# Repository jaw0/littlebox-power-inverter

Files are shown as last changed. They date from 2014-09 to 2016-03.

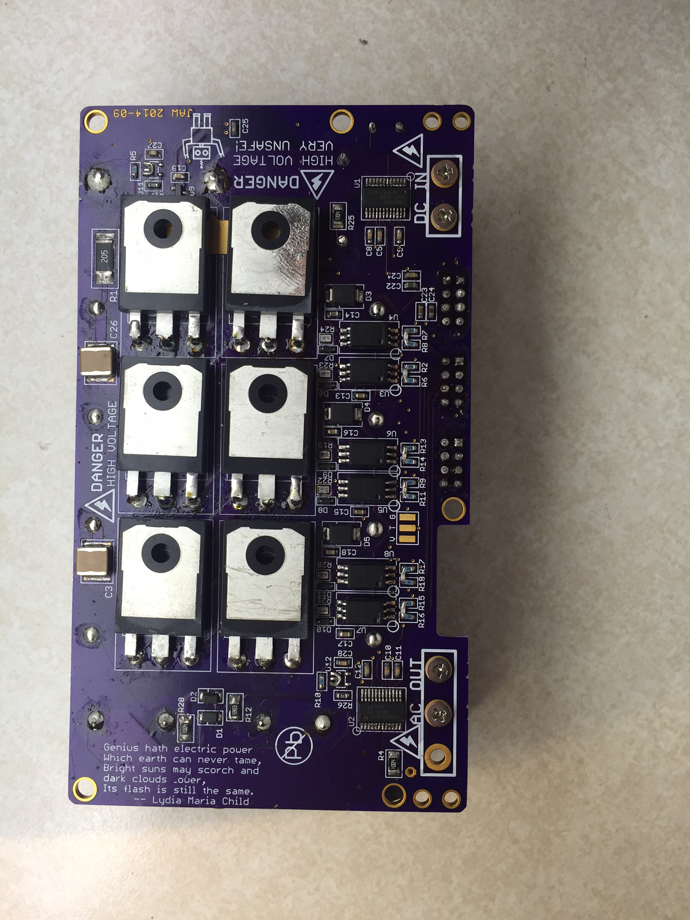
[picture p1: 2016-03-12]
img/IMG_0962.JPG

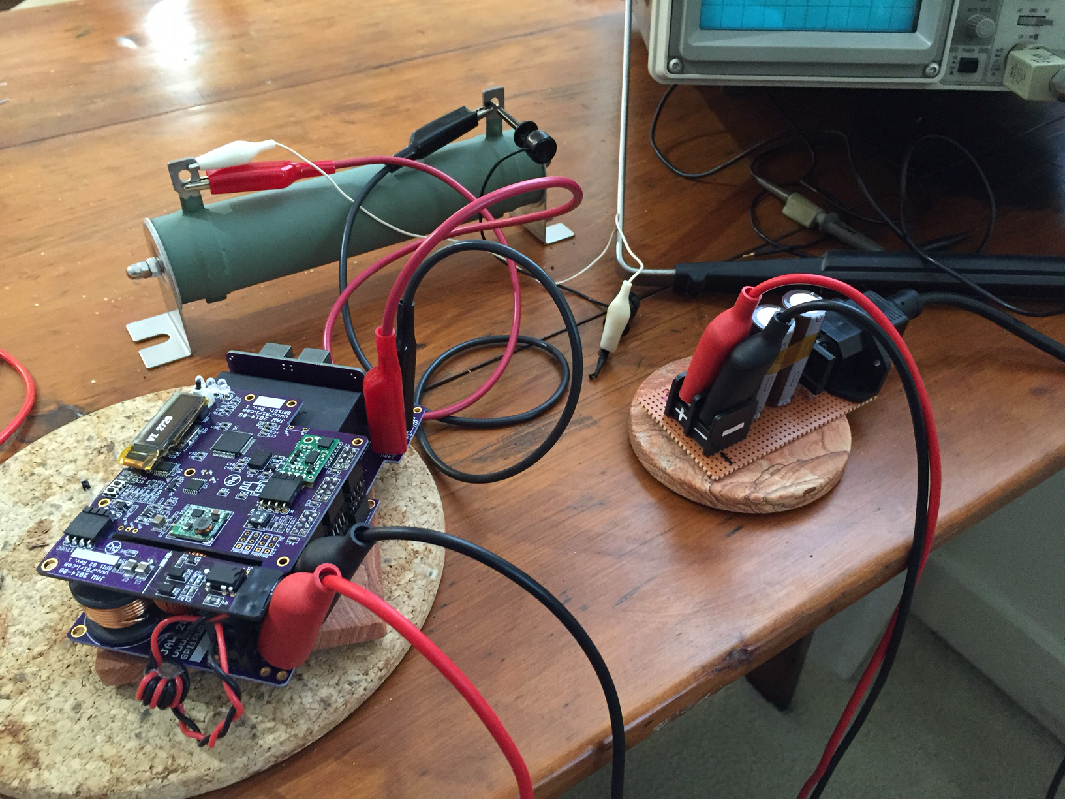
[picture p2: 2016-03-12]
img/IMG_0753.JPG

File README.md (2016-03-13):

google sponsored a contest, [the little box challenge,](https://www.littleboxchallenge.com)
to design a small, efficient, power inverter.

* Must be able to handle up to 2 kVA loads
* Must achieve a power density of equal to or greater than 50 W/in3
* Must be able to handle loads with power factors from 0.7–1, leading and lagging in an islanded mode
* Must be in a rectangular metal enclosure of no more than 40 in3
* Will be taking in 450 V DC power in series with a 10 Ω resistor
* Must output 240 V, 60 Hz AC single phase power
* Must have a total harmonic distortion + noise on both voltage and current of < 5%
* Must have an input ripple current of < 20%
* Must have an input ripple voltage of < 3%
* Must have a DC-AC efficiency of greater than 95%
* Must maintain a temperature of no more than 60°C during operation everywhere on the outside of the device that can be touched.

this is what I came up with. it did not win.

unlike the winning entry, this device uses only
standard, commercially available, off the shelf parts.

* * * * * * * * WARNING * * * * * * * *

This device contains potentially lethal voltages.

This device does not comply with consumer
electrical safety requirements.

DO NOT USE OR BUILD THIS UNLESS YOU ARE FAMILIAR WITH
THE SAFETY PRECAUTIONS FOR WORKING WITH HIGH VOLTAGE.

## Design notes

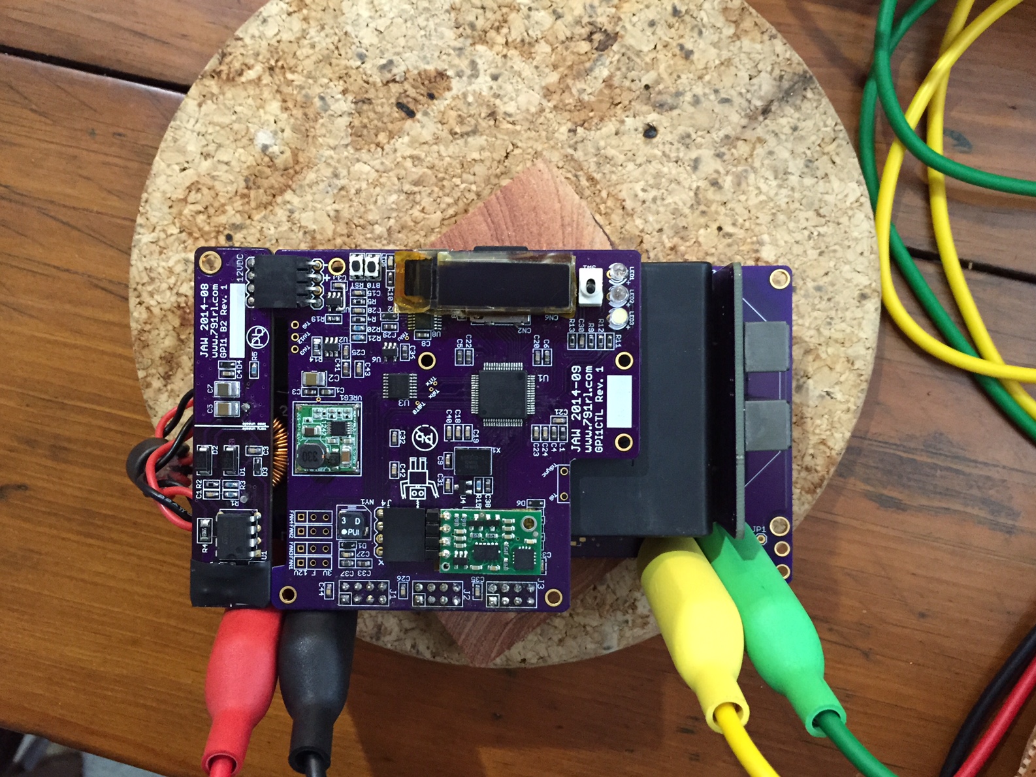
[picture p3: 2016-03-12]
img/inverter.jpg

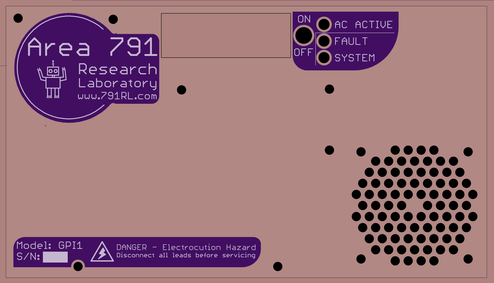
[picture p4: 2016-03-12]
img/cover.png

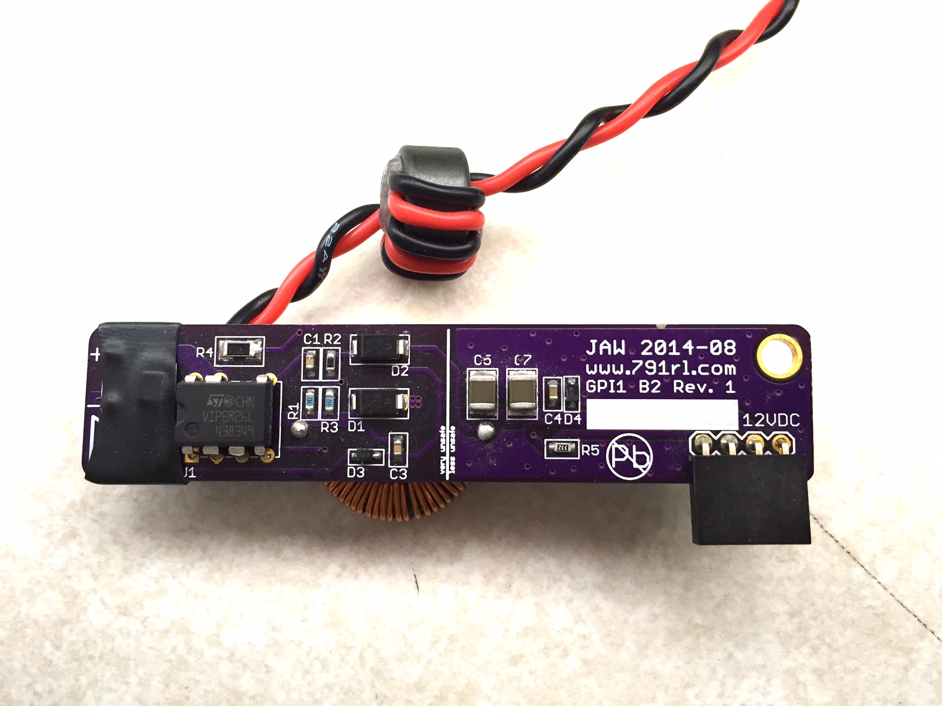
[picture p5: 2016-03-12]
img/powerbrd.jpg

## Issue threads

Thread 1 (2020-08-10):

questions

klasrocket, 2020-08-10:
hi.

been looking into this project to try to find what the lower limit for input voltage is, or maybe its only efficiency dropping?
while looking around I realized that there are 3 different output filters, are they just differnt iterations or is each one for a specific kind of load?
hope you got some time to help me clarify this.

jaw0, 2020-08-10:
the viper chip that steps the voltage down to 12V has a minimum (you'll have to look it up). in testing, I bypassed that and ran it on 12V, not efficient, but functional.

the different filters were just testing to get it smaller, still but good enough.

klasrocket, 2021-09-25:
Thanks for the previous clarifications! I still have not got to the point of starting to build a unit but just revisited this project again.
I have another question that I hope you might want to help me answering.
Do you think it would it be possible to run 3 of your inverters in sync with 120deg offset for 3phase output? My idea is to use some of the unused pins for serial communication, and let 1 of the inverters send the variable "cycle_step" to the other 2 instead of letting them increment that locally.

Closed 2020-08-10.

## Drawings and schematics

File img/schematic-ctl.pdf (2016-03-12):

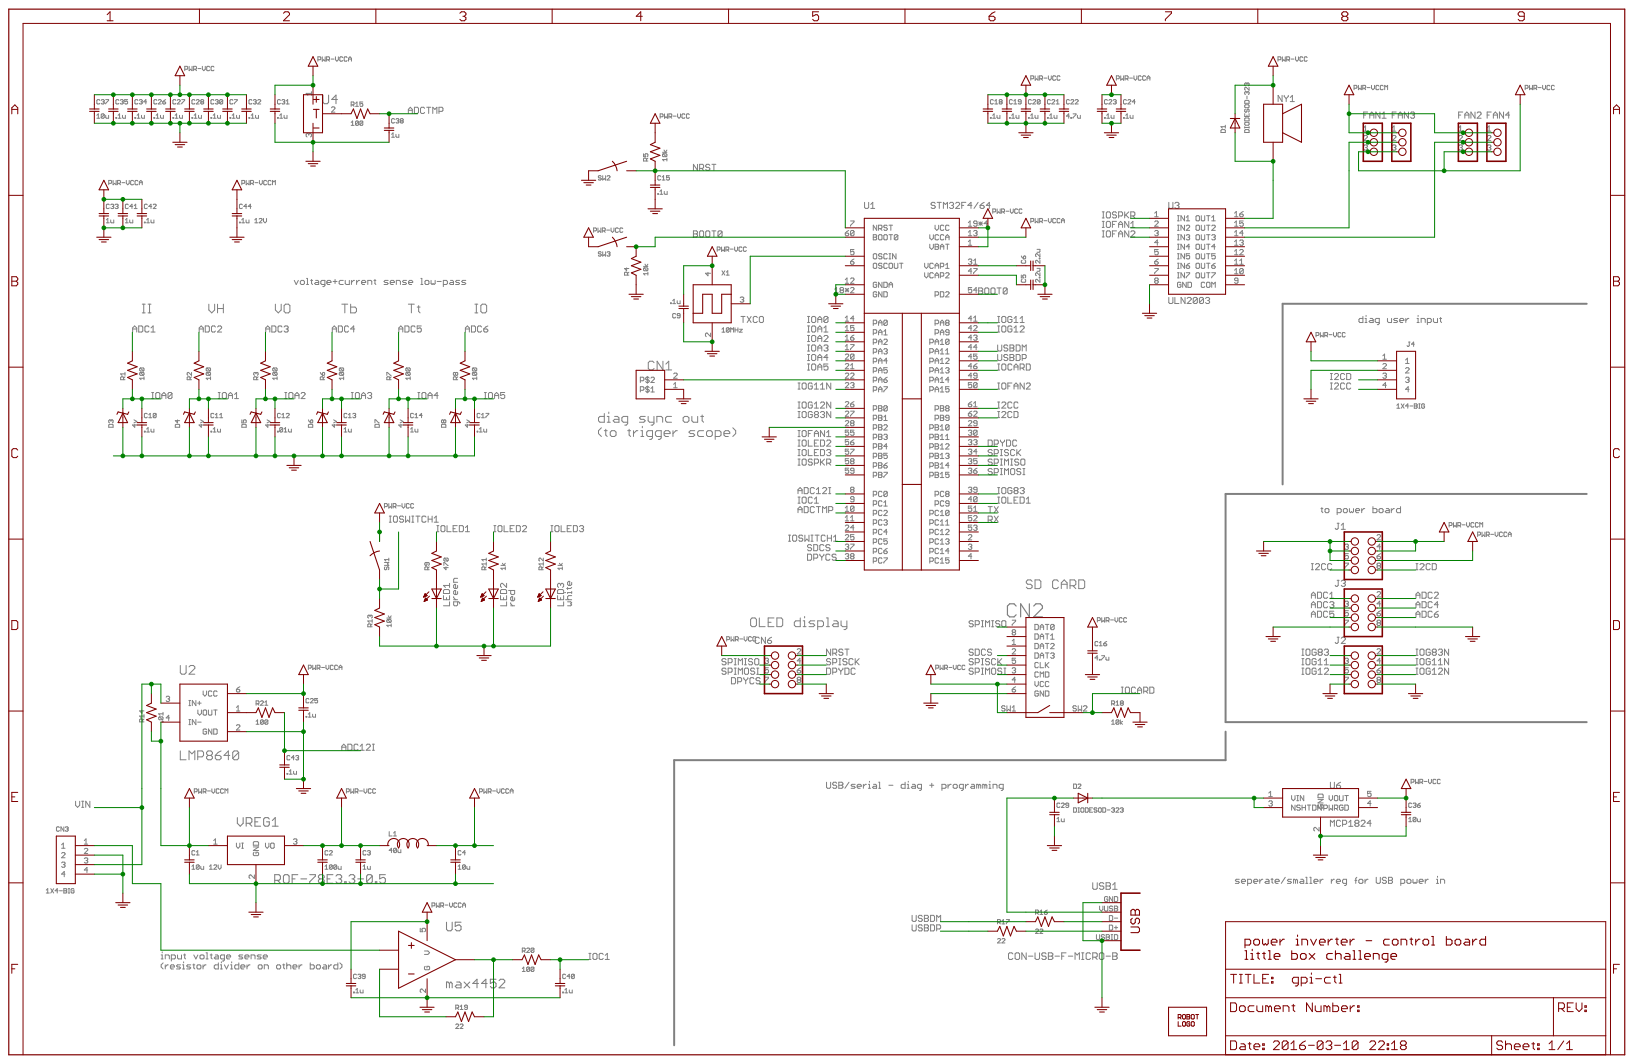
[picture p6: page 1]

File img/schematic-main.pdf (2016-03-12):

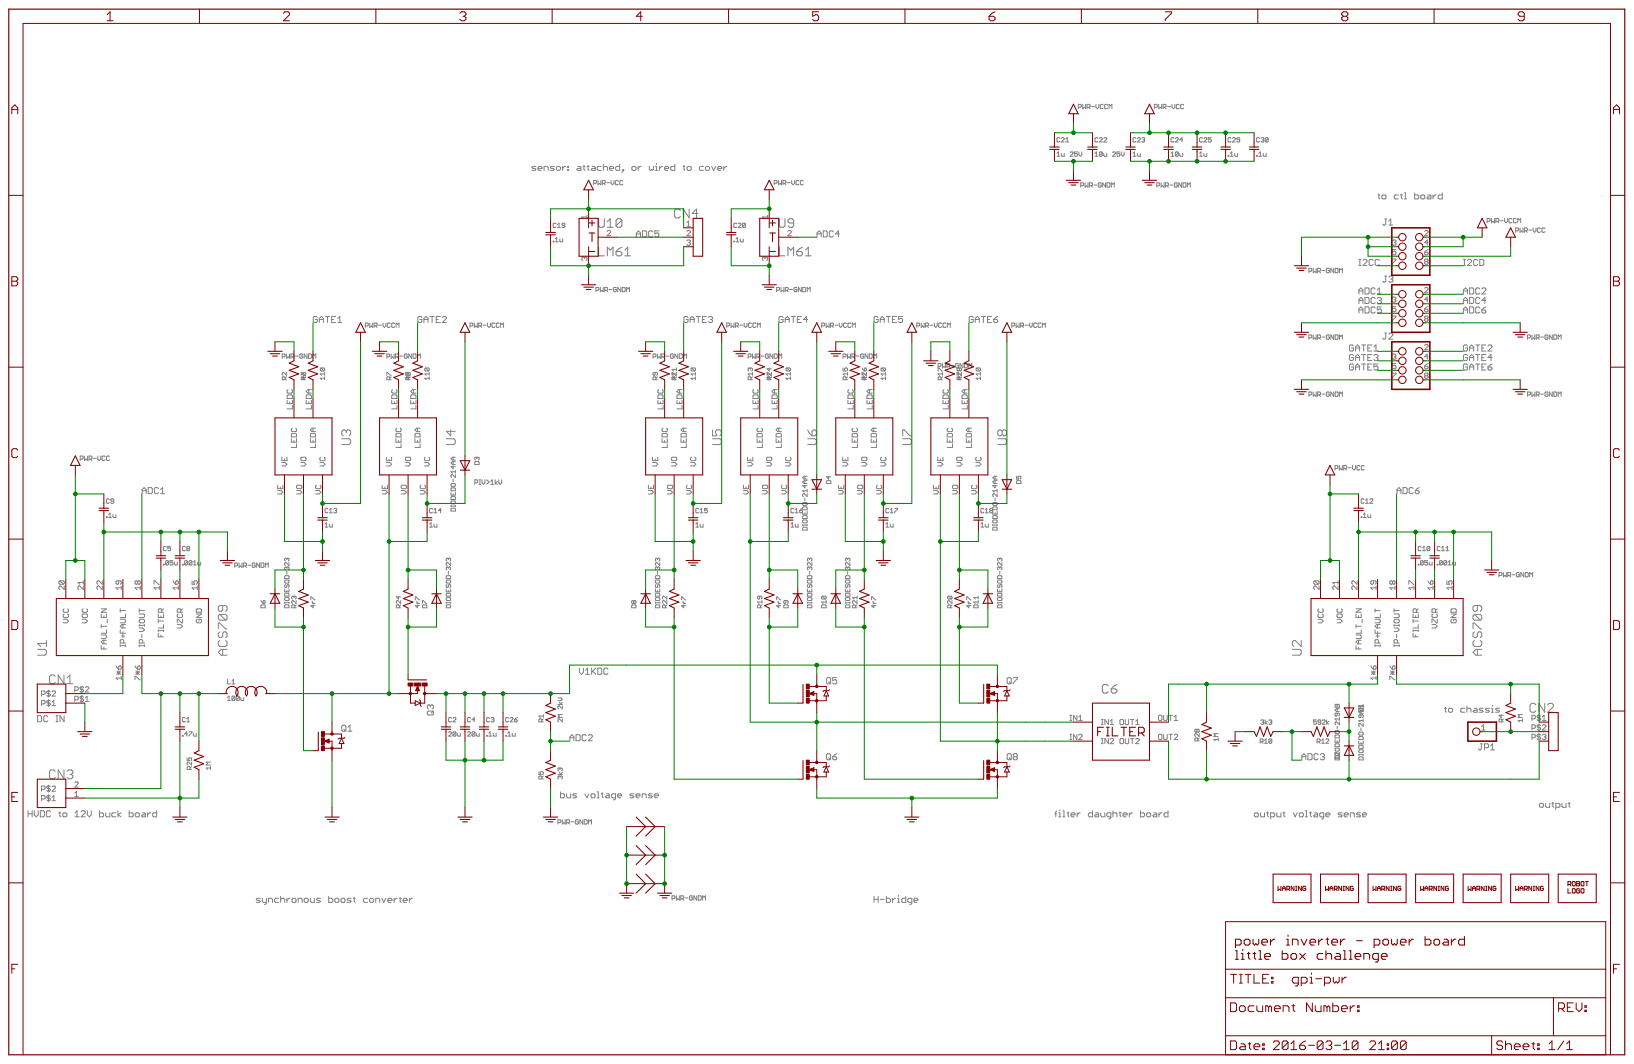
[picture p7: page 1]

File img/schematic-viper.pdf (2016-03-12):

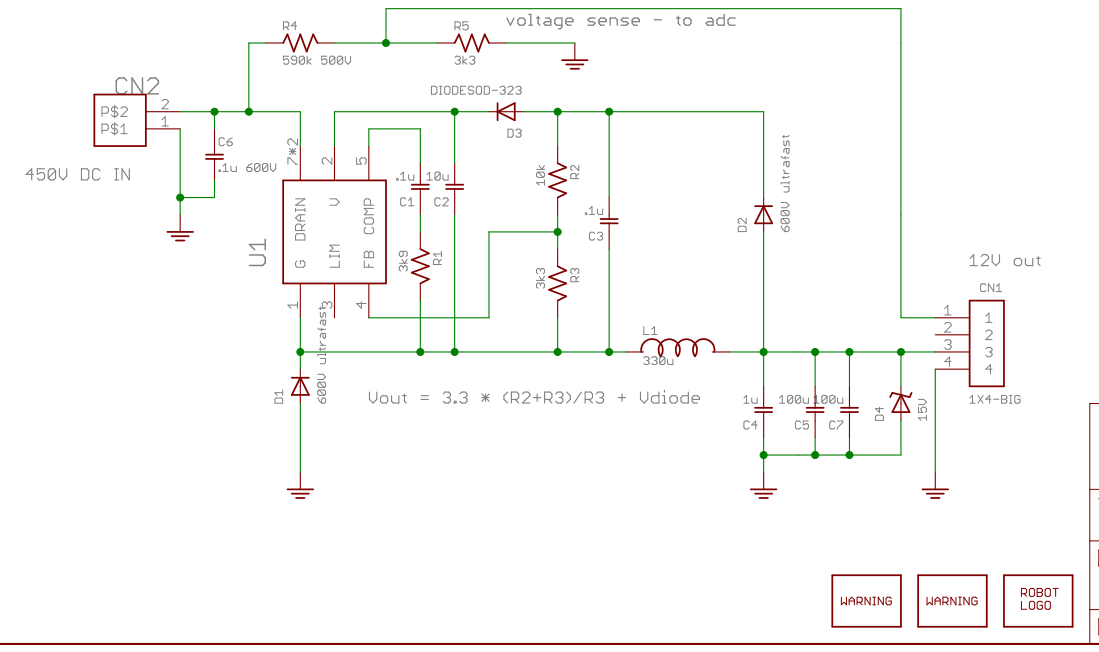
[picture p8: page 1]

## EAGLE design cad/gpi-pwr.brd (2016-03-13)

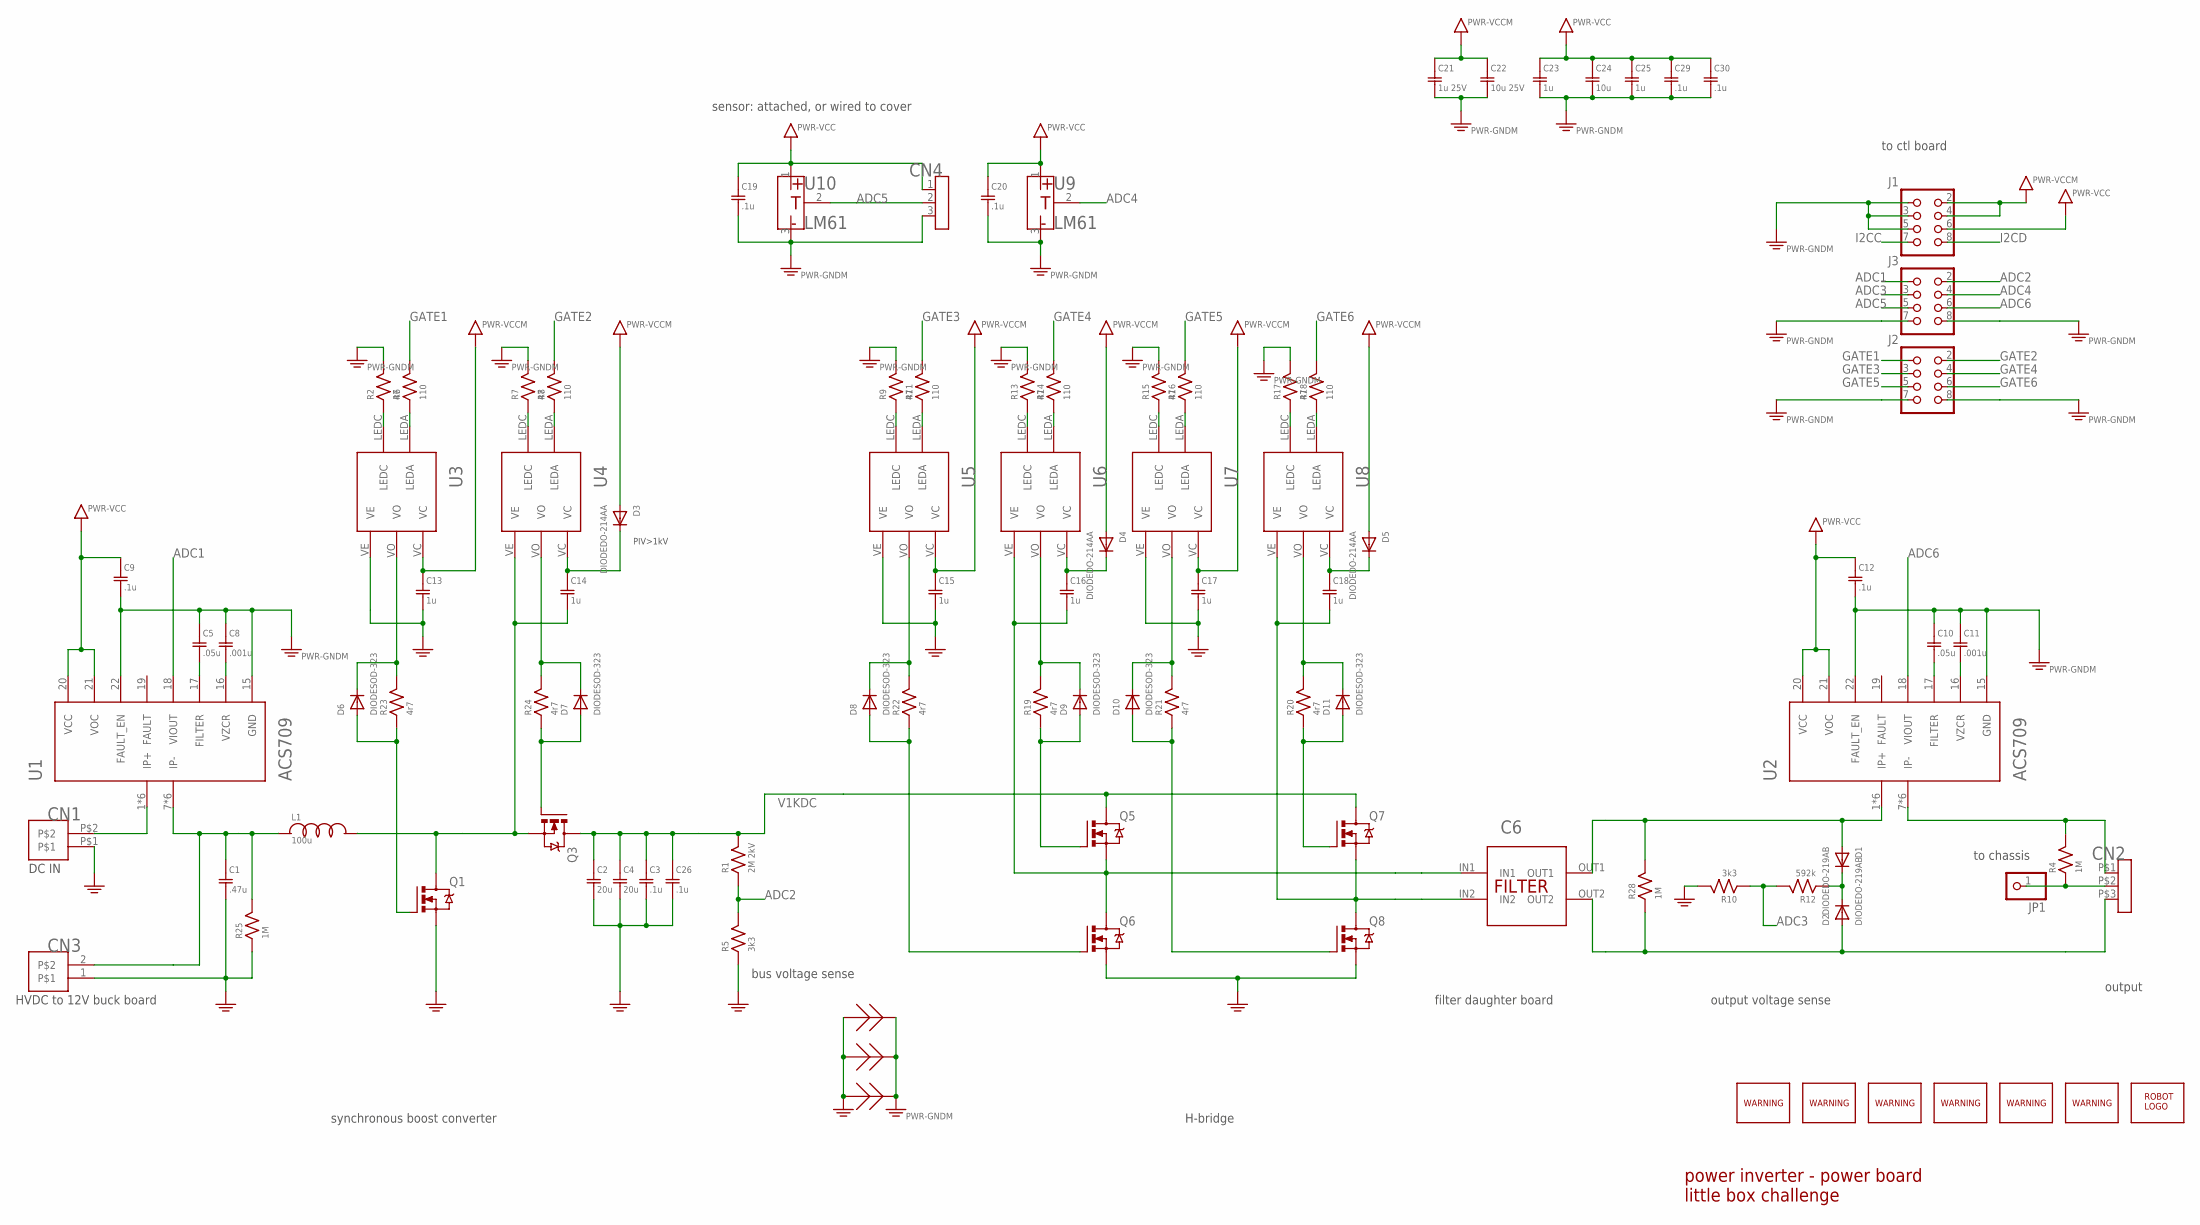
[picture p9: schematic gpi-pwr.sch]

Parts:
C1: .47u; R46KI333000N1M
C2, C4: 20u; MKP1848S62010JY5F
C3, C26: .1u; SMD2220
C5, C10: .05u; SMD0603
C6: FILTER; FILTER-B4R0
C8, C11: .001u; SMD0603
C9, C12, C19, C20, C29, C30: .1u; SMD0603
C13, C14, C15, C16, C17, C18, C23, C25: 1u; SMD0603
C21: 1u 25V; SMD0603
C22: 10u 25V; SMD0603
C24: 10u; SMD0603
CN1: HEADER-1X2; CONN-10AWG-2
CN2: HEADER-3X1; CONN-10AWG-3
CN3: HEADER-1X2.4; HEADER-1X2-THM-WIDE
CN4: HEADER-3X12MM; HEADER-3X1-2SMD
D1, D2: DIODEDO-219AB; DO-219AB
D3, D4, D5: DIODEDO-214AA; DO-214AA
D6, D7, D8, D9, D10, D11: DIODESOD-323; SOD-323
J1, J2, J3: HEADER-2X4; HEADER-2X04
JP1: PINHD-1X1; 1X01
L1: 100u; AIRD03
Q1, Q3, Q5, Q6, Q7, Q8: C2M0160120D; TO-247-3-DOWN
R1: 2M 2kV; SMD2512
R2, R7, R9, R13, R15, R17: 47; SMD0603
R4, R25, R28: 1M; SMD1206
R5, R10: 3k3; SMD0603
R6, R8, R11, R14, R16, R18: 110; SMD0603
R12: 592k; SMD1206
R19, R20, R21, R22, R23, R24: 4r7; SMD0508
U1, U2: ACS709; QSOP24
U3, U4, U5, U6, U7, U8: ACPL-P346P346; ACPL-P346
U9, U10: LM61; SOT-23
U$1: ROBOTMAN-LOGO
U$2, U$3, U$4, U$5, U$6, U$7: SYMBOL-WARNING
Z1, Z2, Z3: SHORT

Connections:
ADC1: J3.1, U1.18 (VIOUT)
ADC2: J3.2, R1.P$1, R5.2
ADC3: J3.3, R10.1, R12.2
ADC4: J3.4, U9.2 (OUT)
ADC5: CN4.2, J3.5, U10.2 (OUT)
ADC6: J3.6, U2.18 (VIOUT)
GATE1: J2.1, R6.2
GATE2: J2.2, R8.2
GATE3: J2.3, R11.2
GATE4: J2.4, R14.2
GATE5: J2.5, R16.2
GATE6: J2.6, R18.2
GND: C1.P$2, C2.2A, C2.2B, C3.P$2, C4.2A, C4.2B, C13.2, C15.2, C17.2, C26.P$2, CN1.P$1, CN3.1, Q1.3 (S), Q6.3 (S), Q8.3 (S), R5.1, R10.2, R25.1, U3.VE, U5.VE, U7.VE, Z1.P$1, Z2.P$1, Z3.P$1
GNDM: C5.1, C8.1, C9.2, C10.1, C11.1, C12.2, C19.2, C20.2, C21.2, C22.2, C23.2, C24.2, C25.2, C29.2, C30.2, CN4.3, J1.1, J1.3, J1.5, J2.7, J2.8, J3.7, J3.8, R2.2, R7.2, R9.2, R13.2, R15.2, R17.2, U1.15 (GND), U1.22 (FAULT_EN), U2.15 (GND), U2.22 (FAULT_EN), U9.3 (G), U10.3 (G), Z1.P$2, Z2.P$2, Z3.P$2
I2CC: J1.7
I2CD: J1.8
unnamed: CN1.P$2, U1.1 (IP+), U1.2 (IP+), U1.3 (IP+), U1.4 (IP+), U1.5 (IP+), U1.6 (IP+)
unnamed: D9.C, R19.P$2, U6.VO
unnamed: C14.2, L1.P$2, Q1.2 (D), Q3.3 (S), U4.VE
unnamed: D6.A, Q1.1 (G), R23.P$1
unnamed: D6.C, R23.P$2, U3.VO
unnamed: C1.P$1, CN3.2, L1.P$1, R25.2, U1.7 (IP-), U1.8 (IP-), U1.9 (IP-), U1.10 (IP-), U1.11 (IP-), U1.12 (IP-)
unnamed: D1.C, D2.C, R12.1
unnamed: CN2.P$1 (1), R4.2, U2.7 (IP-), U2.8 (IP-), U2.9 (IP-), U2.10 (IP-), U2.11 (IP-), U2.12 (IP-)
unnamed: CN2.P$2 (2), JP1.1, R4.1
unnamed: C5.2, U1.17 (FILTER)
unnamed: C8.2, U1.16 (VZCR)
unnamed: C10.2, U2.17 (FILTER)
unnamed: C6.IN1, C16.2, Q5.3 (S), Q6.2 (D), U6.VE
unnamed: C6.IN2, C18.2, Q7.3 (S), Q8.2 (D), U8.VE
unnamed: C11.2, U2.16 (VZCR)
unnamed: C14.1, D3.C, U4.VC
unnamed: D9.A, Q5.1 (G), R19.P$1
unnamed: D8.A, Q6.1 (G), R22.P$1
unnamed: D10.A, Q8.1 (G), R21.P$1
unnamed: D11.A, Q7.1 (G), R20.P$1
unnamed: R2.1, U3.LEDC
unnamed: C6.OUT1, D1.A, R28.2, U2.1 (IP+), U2.2 (IP+), U2.3 (IP+), U2.4 (IP+), U2.5 (IP+), U2.6 (IP+)
unnamed: C6.OUT2, CN2.P$3 (3), D2.A, R28.1
unnamed: C16.1, D4.C, U6.VC
unnamed: R6.1, U3.LEDA
unnamed: C18.1, D5.C, U8.VC
unnamed: R7.1, U4.LEDC
unnamed: R8.1, U4.LEDA
unnamed: R9.1, U5.LEDC
unnamed: R11.1, U5.LEDA
unnamed: R13.1, U6.LEDC
unnamed: R14.1, U6.LEDA
unnamed: R15.1, U7.LEDC
unnamed: R16.1, U7.LEDA
unnamed: R17.1, U8.LEDC
unnamed: R18.1, U8.LEDA
unnamed: D11.C, R20.P$2, U8.VO
unnamed: D8.C, R22.P$2, U5.VO
unnamed: D10.C, R21.P$2, U7.VO
unnamed: D7.C, R24.P$2, U4.VO
unnamed: D7.A, Q3.1 (G), R24.P$1
V1KDC: C2.1A, C2.1B, C3.P$1, C4.1A, C4.1B, C26.P$1, Q3.2 (D), Q5.2 (D), Q7.2 (D), R1.P$2
VCC: C9.1, C12.1, C19.1, C20.1, C23.1, C24.1, C25.1, C29.1, C30.1, CN4.1, J1.6, U1.20 (VCC), U1.21 (VOC), U2.20 (VCC), U2.21 (VOC), U9.1 (V), U10.1 (V)
VCCM: C13.1, C15.1, C17.1, C21.1, C22.1, D3.A, D4.A, D5.A, J1.2, J1.4, U3.VC, U5.VC, U7.VC

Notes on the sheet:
PIV>1kV
DC IN
HVDC to 12V buck board
to chassis
sensor: attached, or wired to cover
synchronous boost converter
H-bridge
output
output voltage sense
to ctl board
power inverter - power board little box challenge
filter daughter board
bus voltage sense

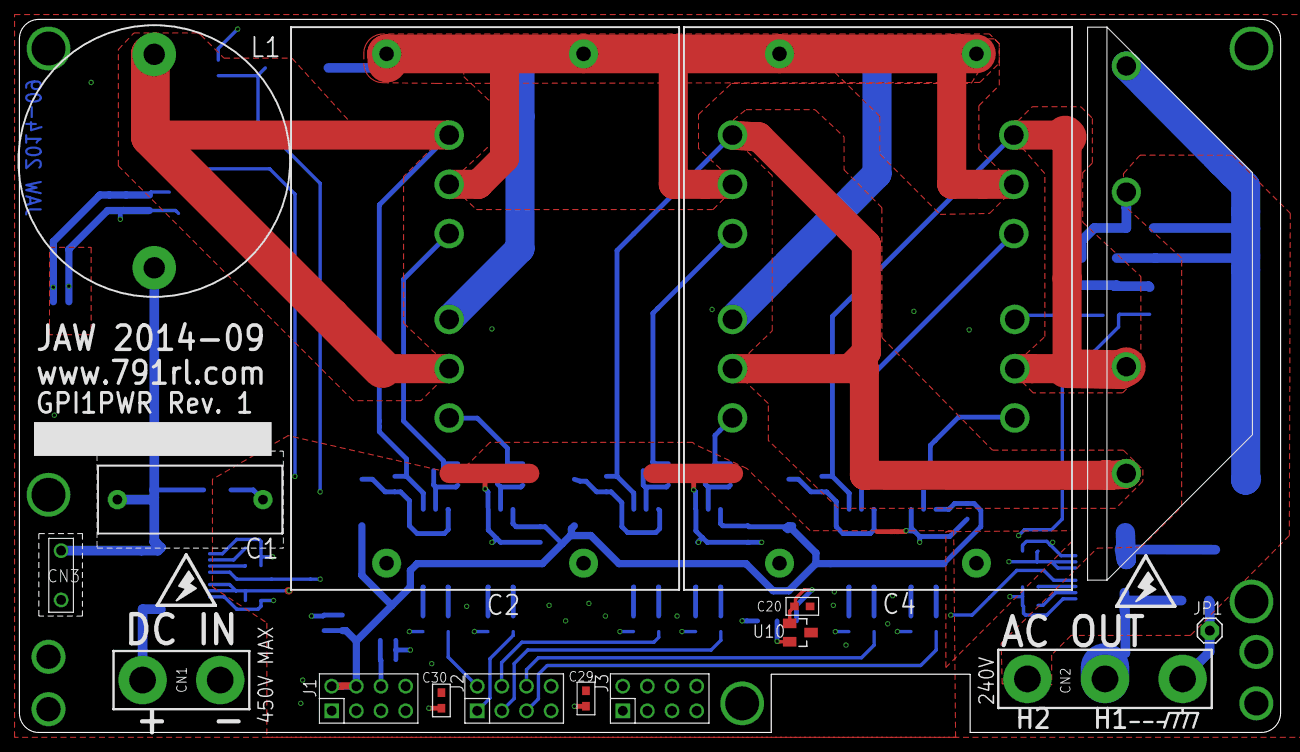
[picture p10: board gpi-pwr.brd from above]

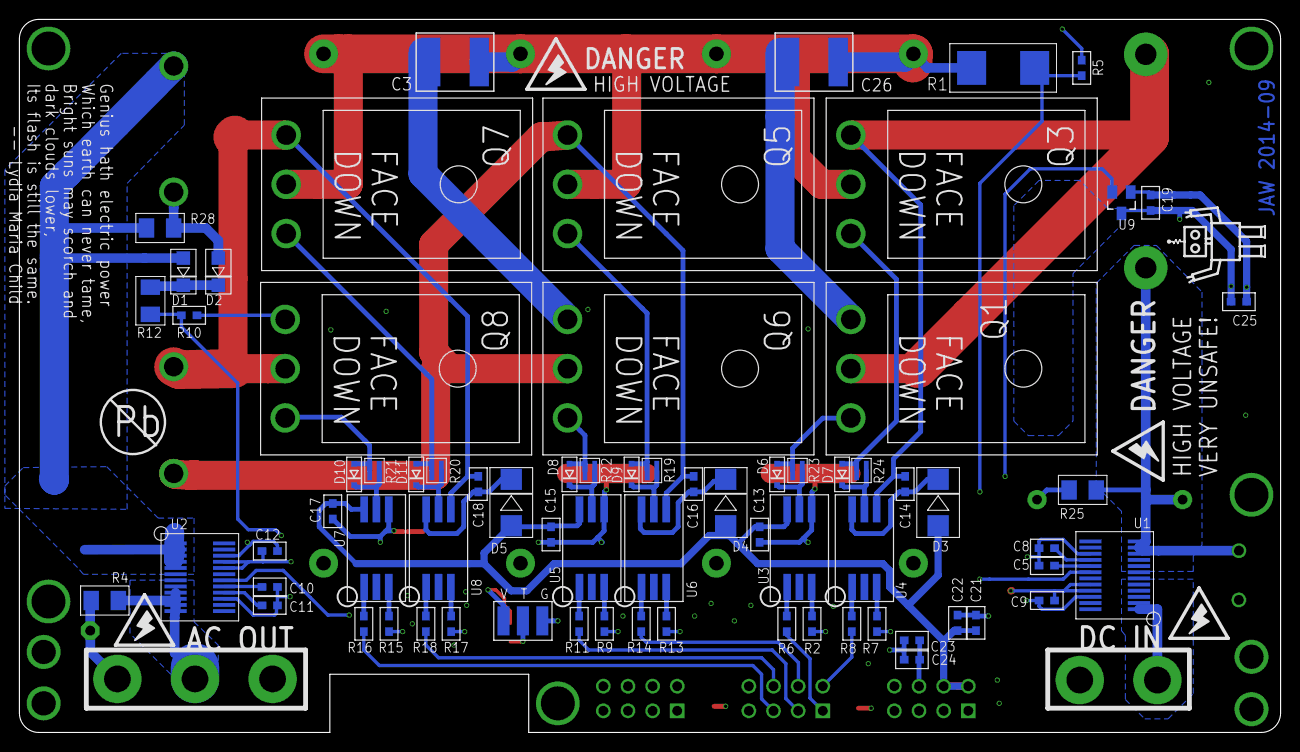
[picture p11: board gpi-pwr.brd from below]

Board: 4 copper layers, 130.0 x 73.5 mm, 98 parts (77 on the bottom side), 58 nets.

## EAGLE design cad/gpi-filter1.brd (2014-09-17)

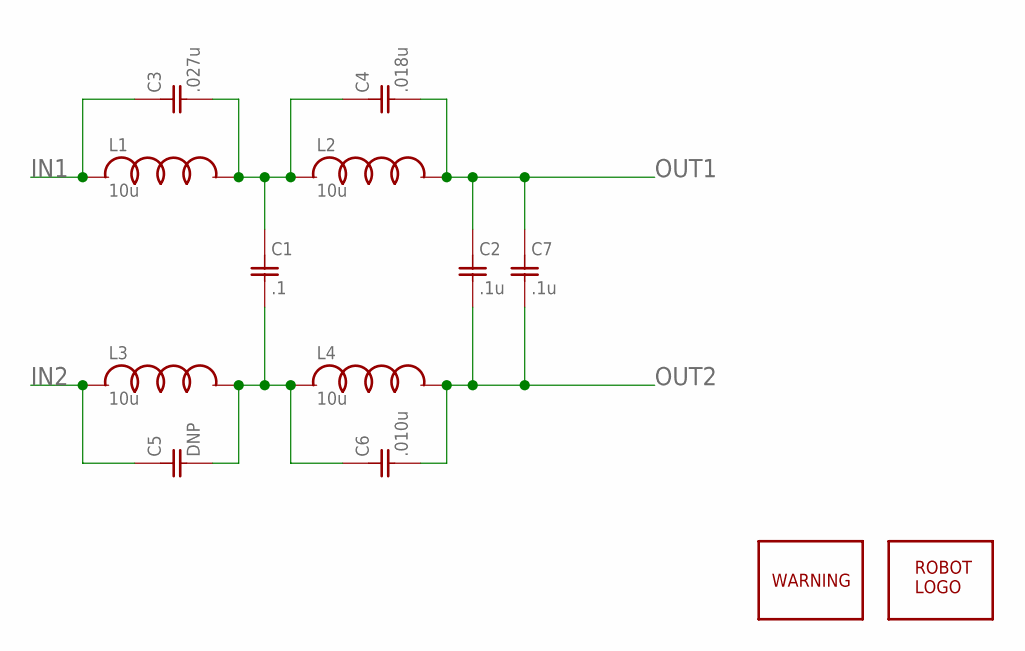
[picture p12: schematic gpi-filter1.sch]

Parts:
C1: .1; SMD1210
C2, C7: .1u; SMD1210
C3: .027u; SMD1210
C4: .018u; SMD1210
C5: DNP; SMD1210
C6: .010u; SMD1210
L1, L2, L3, L4: 10u; XAL10
U$1: ROBOTMAN-LOGO
U$2: SYMBOL-WARNING

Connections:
IN1: C3.1, L1.P$1
IN2: C5.1, L3.P$1
unnamed: C1.1, C3.2, C4.1, L1.P$2, L2.P$1
unnamed: C1.2, C5.2, C6.1, L3.P$2, L4.P$1
OUT1: C2.1, C4.2, C7.1, L2.P$2
OUT2: C2.2, C6.2, C7.2, L4.P$2

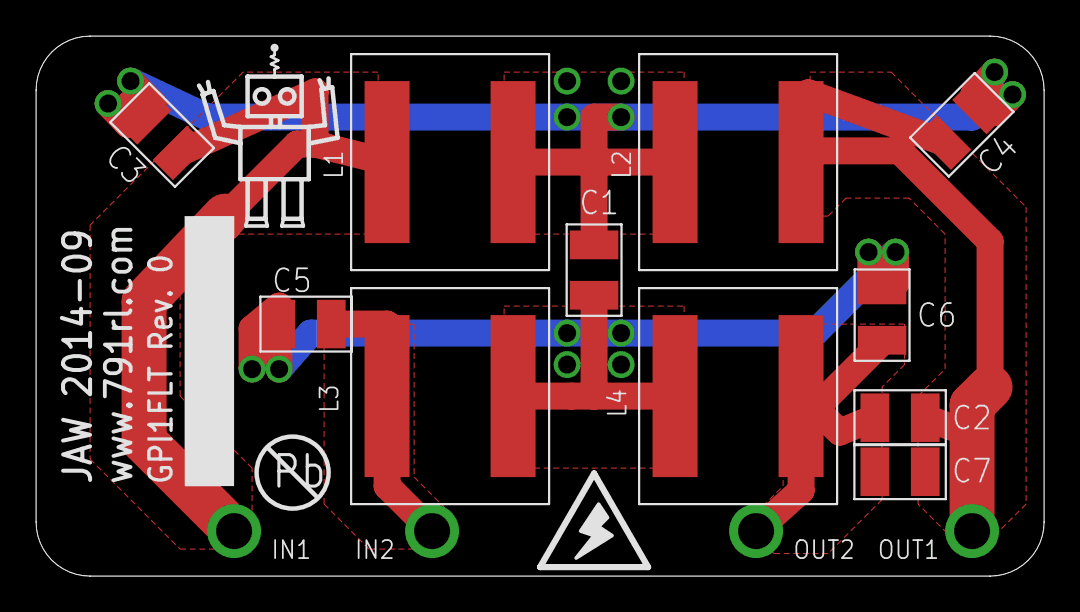
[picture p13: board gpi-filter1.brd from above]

Board: 2 copper layers, 56.0 x 30.0 mm, 13 parts (0 on the bottom side), 6 nets.

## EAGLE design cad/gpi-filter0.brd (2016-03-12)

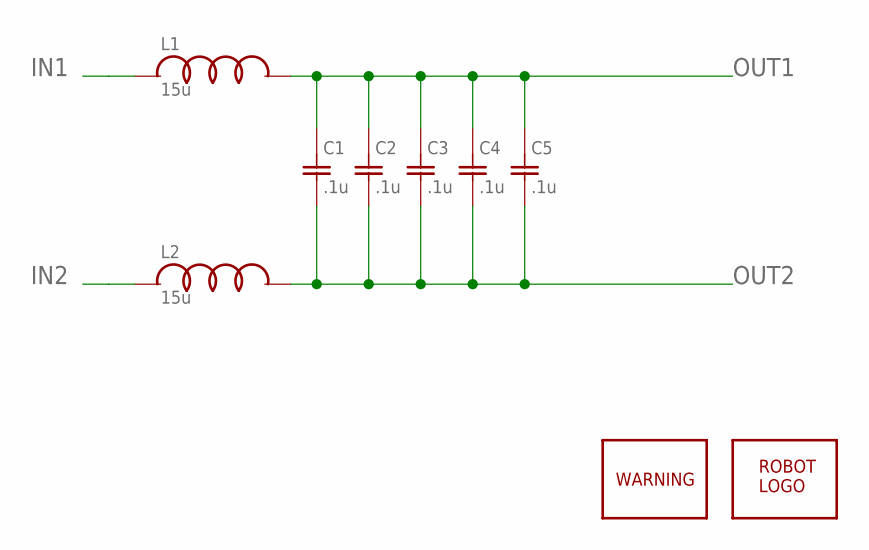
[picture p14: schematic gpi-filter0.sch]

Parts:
C1, C2, C3, C4, C5: .1u; SMD1210
L1, L2: 15u; BOURNS2303H
U$1: ROBOTMAN-LOGO
U$2: SYMBOL-WARNING

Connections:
IN1: L1.P$1
IN2: L2.P$1
OUT1: C1.1, C2.1, C3.1, C4.1, C5.1, L1.P$2
OUT2: C1.2, C2.2, C3.2, C4.2, C5.2, L2.P$2

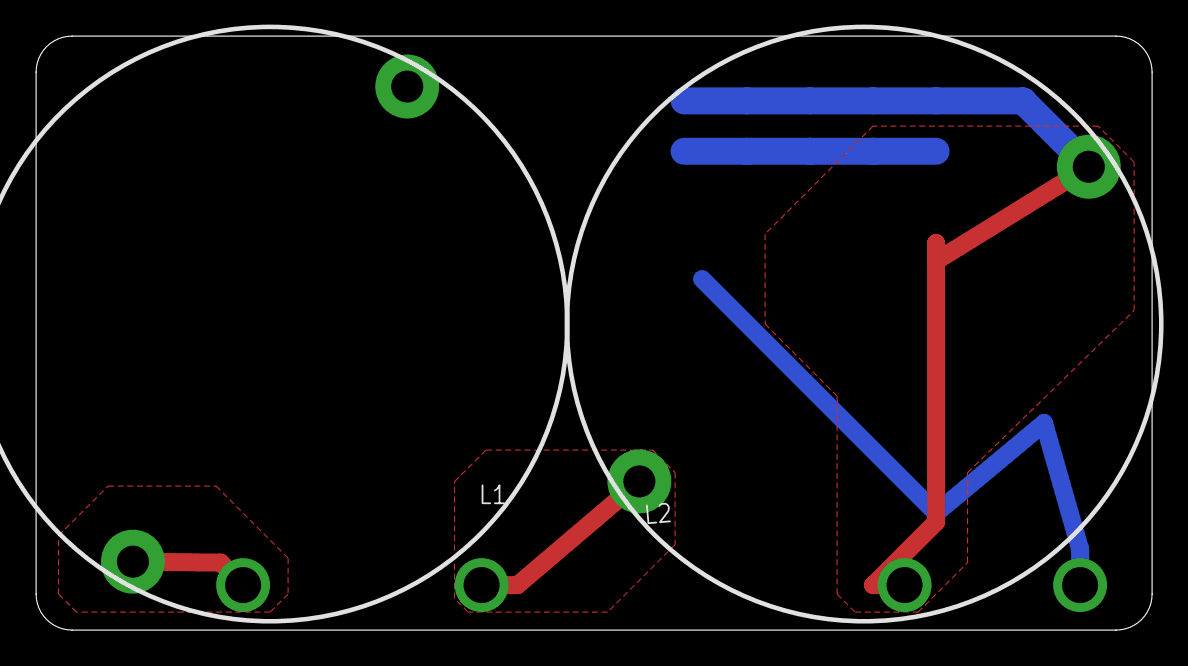
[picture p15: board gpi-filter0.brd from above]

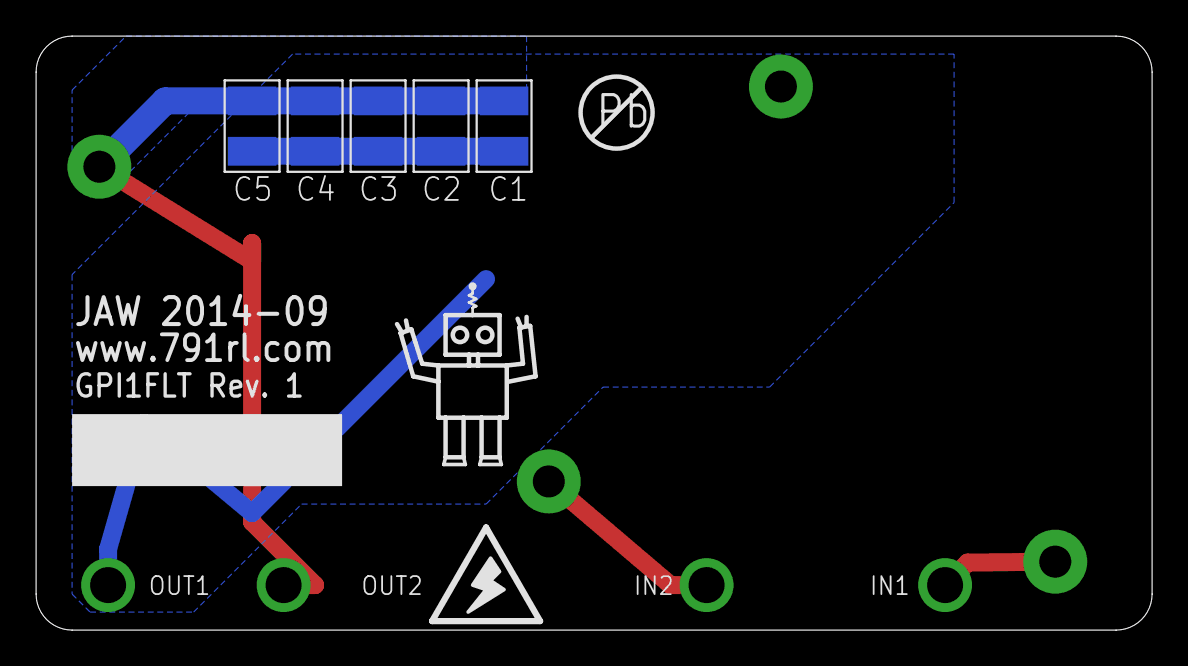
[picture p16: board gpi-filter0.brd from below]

Board: 2 copper layers, 62.0 x 33.0 mm, 9 parts (7 on the bottom side), 2 nets.

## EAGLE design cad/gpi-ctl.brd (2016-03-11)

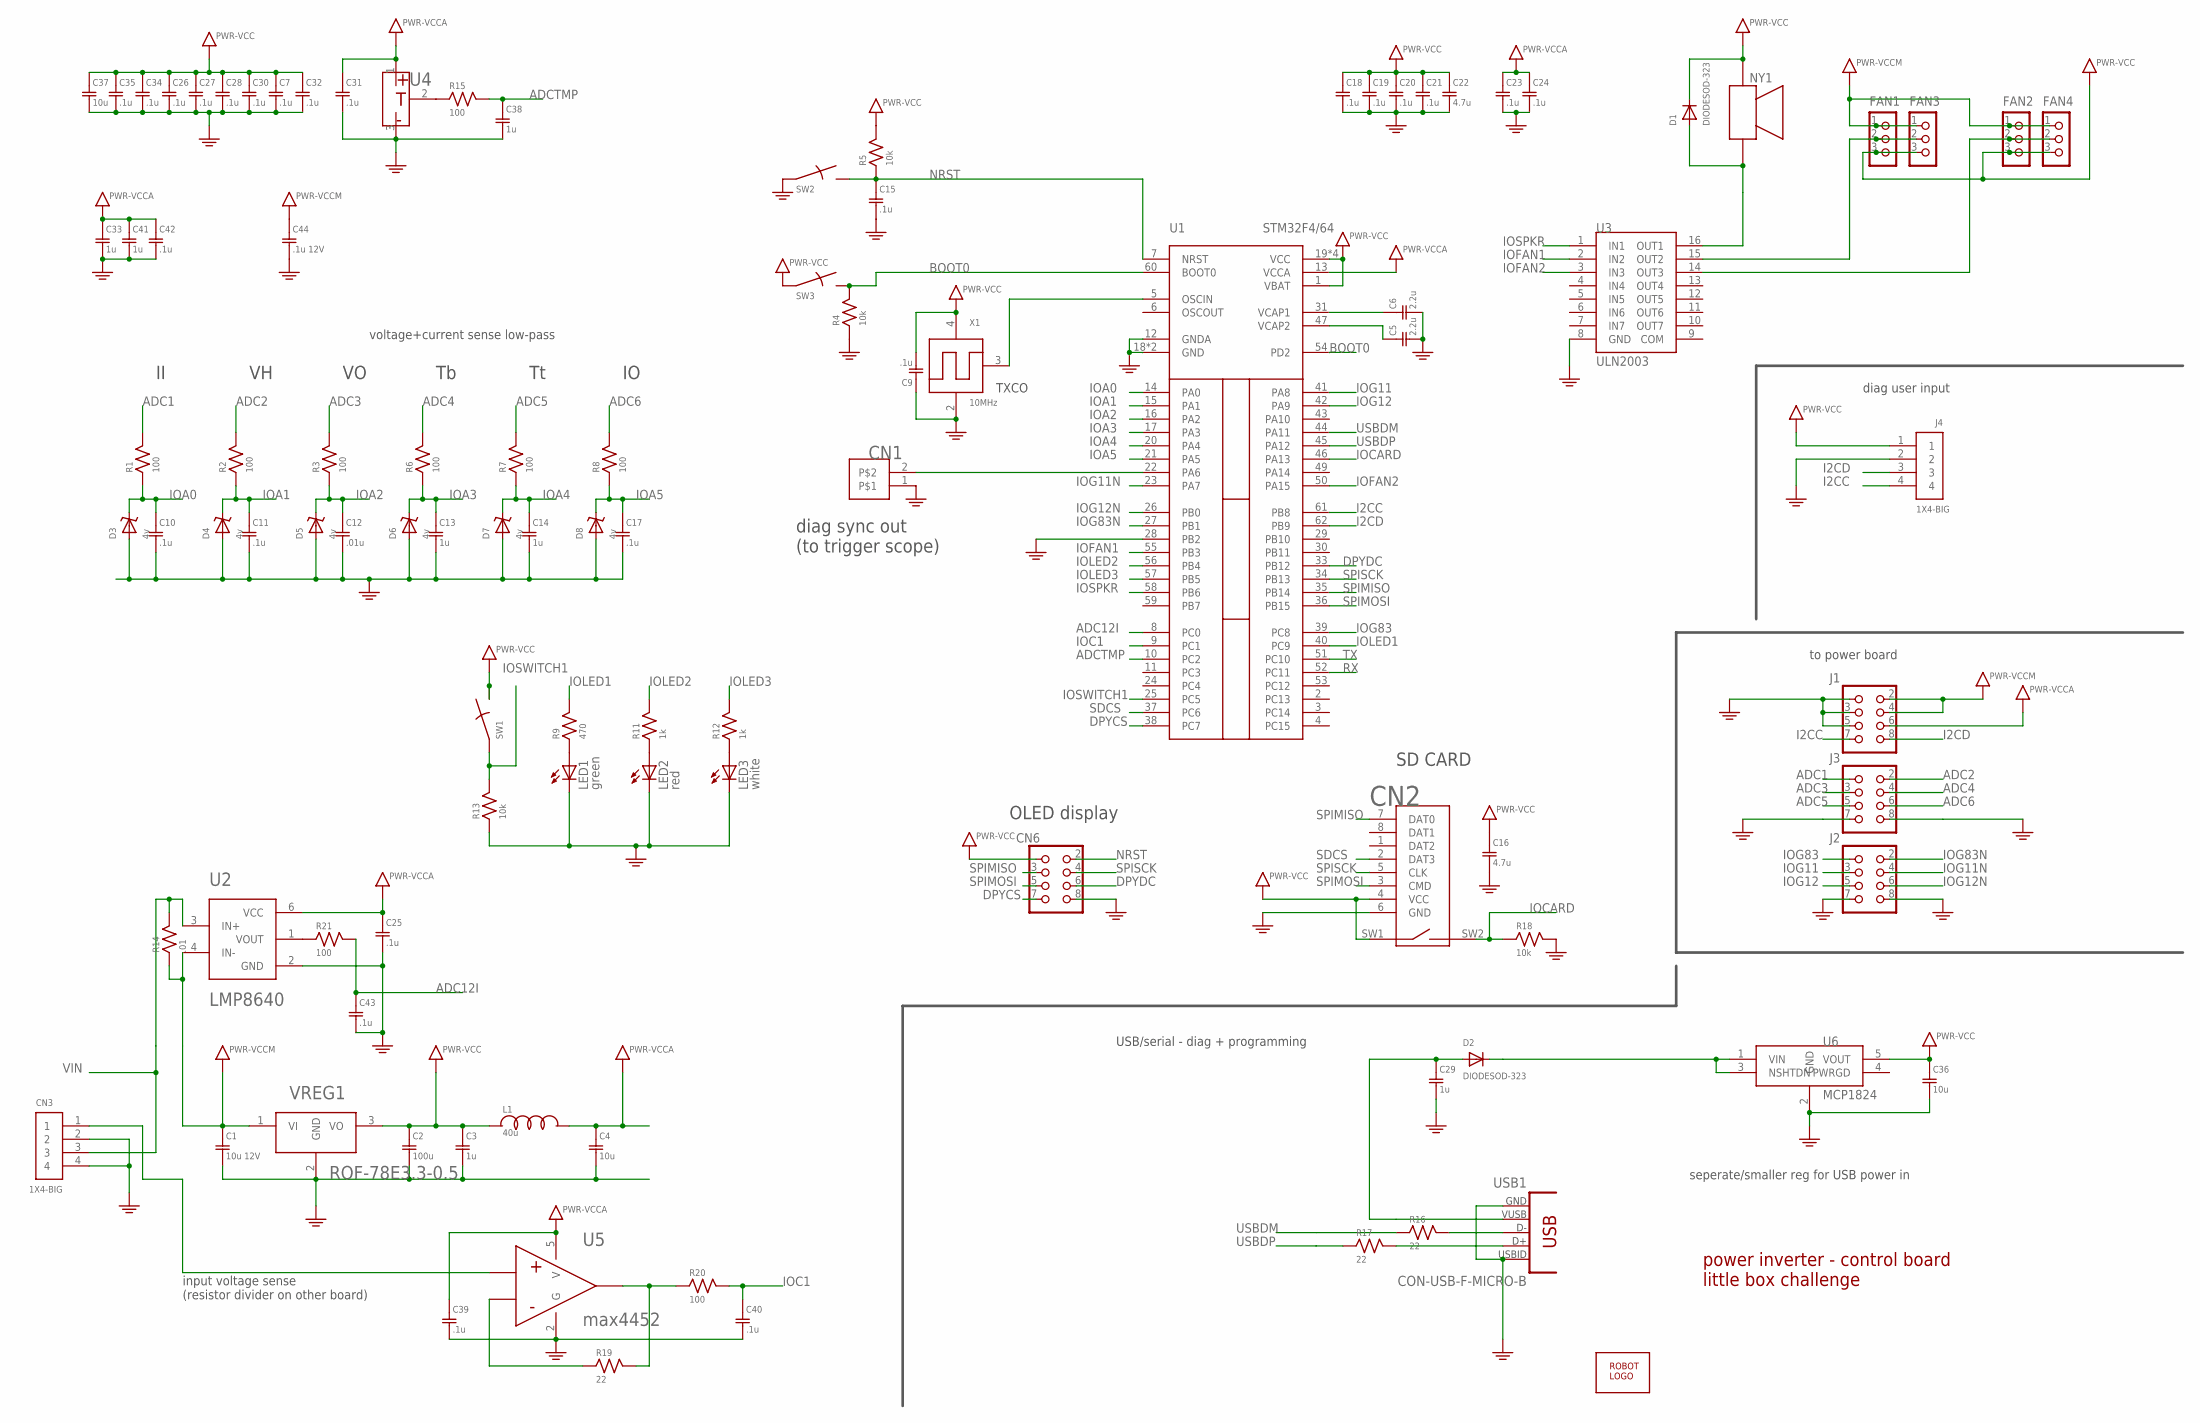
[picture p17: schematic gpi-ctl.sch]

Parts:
C1: 10u 12V; SMD0603
C2: 100u; SMD1210
C3, C13, C14, C29, C33, C38, C41: 1u; SMD0603
C4, C36, C37: 10u; SMD0603
C5, C6: 2.2u; SMD0603
C7, C9, C10, C11, C15, C17, C18, C19, C20, C21, C23, C24, C25, C26, C27, C28, C30, C31, C32, C34, C35, C39, C40, C42, C43: .1u; SMD0603
C12: .01u; SMD0603
C16, C22: 4.7u; SMD0603
C44: .1u 12V; SMD0603
CN1: HEADER-1X2.4; HEADER-1X2-THM-WIDE
CN2: MICROSDPLAIN; MICROSD/MOLEX/FRONT/PLAIN
CN3: 1X4-BIG; 1X04-BIG
CN6: HEADER-2X4; HEADER-2X04
D1, D2: DIODESOD-323; SOD-323
D3, D4, D5, D6, D7, D8: 4v; SOD-323
FAN1, FAN2, FAN3, FAN4: CON_HEADER_1X03-PTH; M1X3
J1, J2, J3: HEADER-2X4; HEADER-2X04
J4: 1X4-BIG; 1X04-BIG
L1: 40u; SMD0603
LED1: green; LED3MM
LED2: red; LED3MM
LED3: white; LED3MM
NY1: PUI-5040; PUI-0540
R1, R2, R3, R6, R7, R8, R15, R20, R21: 100; SMD0603
R4, R5, R13, R18: 10k; SMD0603
R9: 470; SMD0603
R11, R12: 1k; SMD0603
R14: .01; SMD0805
R16, R17, R19: 22; SMD0603
SW1: SWITCHGT12-THOLE; SWITCH-GT12MCBE
SW2, SW3: SWITCHKMR211; KMR211
U1: STM32F4/64; TQFP64
U2: LMP8640; SOT-6
U3: ULN2003; TSSOP-16
U4: TEMPERATURE; SOT-23
U5: max4452; SOT-23-5
U6: MCP1824; SOT-23-5
U$1: ROBOTMAN-LOGO
USB1: CON-USB-F-MICRO-B; CONN_USB_MICRO-B
VREG1: ROF-78E3.3-0.5; ROF7800
X1: 10MHz; OSC-AST3TQ

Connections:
ADC1: J3.1, R1.2
ADC2: J3.2, R2.2
ADC3: J3.3, R3.2
ADC4: J3.4, R6.2
ADC5: J3.5, R7.2
ADC6: J3.6, R8.2
ADC12I: C43.1, R21.2, U1.8 (PC0)
ADCTMP: C38.1, R15.2, U1.10 (PC2)
BOOT0: R4.2, SW3.2, SW3.4, U1.54 (PD2), U1.60 (BOOT0)
DPYCS: CN6.7, U1.38 (PC7)
DPYDC: CN6.6, U1.33 (PB12)
GND: C1.2, C2.2, C3.2, C4.2, C5.2, C6.2, C7.2, C9.1, C10.2, C11.2, C12.2, C13.2, C14.2, C15.2, C16.2, C17.2, C18.2, C19.2, C20.2, C21.2, C22.2, C23.2, C24.2, C25.2, C26.2, C27.2, C28.2, C29.2, C30.2, C31.2, C32.2, C33.2, C34.2, C35.2, C36.2, C37.2, C38.2, C39.2, C40.2, C41.2, C42.2, C43.2, C44.2, CN1.1, CN2.6 (GND), CN3.2, CN3.4, CN6.8, D3.A, D4.A, D5.A, D6.A, D7.A, D8.A, J1.1, J1.3, J1.5, J2.7, J2.8, J3.7, J3.8, J4.2, LED1.K (C), LED2.K (C), LED3.K (C), R4.1, R13.1, R18.2, SW2.1, SW2.3, U1.12 (GNDA), U1.18 (GND), U1.28 (PB2), U1.63 (GND), U2.2 (GND), U3.8 (GND), U4.3 (G), U5.2 (G), U6.2 (GND), USB1.P4 (USBID), USB1.P5 (GND), VREG1.2 (GND), X1.2 (GND)
I2CC: J1.7, J4.4, U1.61 (PB8)
I2CD: J1.8, J4.3, U1.62 (PB9)
IOA0: C10.1, D3.C, R1.1, U1.14 (PA0)
IOA1: C11.1, D4.C, R2.1, U1.15 (PA1)
IOA2: C12.1, D5.C, R3.1, U1.16 (PA2)
IOA3: C13.1, D6.C, R6.1, U1.17 (PA3)
IOA4: C14.1, D7.C, R7.1, U1.20 (PA4)
IOA5: C17.1, D8.C, R8.1, U1.21 (PA5)
IOC1: C40.1, R20.2, U1.9 (PC1)
IOCARD: CN2.SW2, R18.1, U1.46 (PA13)
IOFAN1: U1.55 (PB3), U3.2 (IN2)
IOFAN2: U1.50 (PA15), U3.3 (IN3)
IOG11: J2.3, U1.41 (PA8)
IOG11N: J2.4, U1.23 (PA7)
IOG12: J2.5, U1.42 (PA9)
IOG12N: J2.6, U1.26 (PB0)
IOG83: J2.1, U1.39 (PC8)
IOG83N: J2.2, U1.27 (PB1)
IOLED1: R9.2, U1.40 (PC9)
IOLED2: R11.2, U1.56 (PB4)
IOLED3: R12.2, U1.57 (PB5)
IOSPKR: U1.58 (PB6), U3.1 (IN1)
IOSWITCH1: R13.2, SW1.1, U1.25 (PC5)
unnamed: FAN2.2, FAN4.2, U3.14 (OUT3)
unnamed: R17.2, USB1.P3 (D+)
unnamed: U1.5 (OSCIN), X1.3 (OSC)
unnamed: R16.2, USB1.P2 (D-)
unnamed: FAN1.2, FAN3.2, U3.15 (OUT2)
unnamed: D2.C, U6.1 (VIN), U6.3 (NSHTDN)
unnamed: R15.1, U4.2 (OUT)
unnamed: R19.1, U5.4 (INM)
unnamed: R19.2, R20.1, U5.1 (OUT)
unnamed: CN1.2, U1.22 (PA6)
unnamed: CN3.1, U5.3 (INP)
unnamed: LED1.A, R9.1
unnamed: LED2.A, R11.1
unnamed: LED3.A, R12.1
unnamed: R21.1, U2.1 (VOUT)
unnamed: C6.1, U1.31 (VCAP1)
unnamed: C5.1, U1.47 (VCAP2)
NRST: C15.1, CN6.2, R5.1, SW2.2, SW2.4, U1.7 (NRST)
RX: U1.52 (PC11)
SDCS: CN2.2 (DAT3), U1.37 (PC6)
SPIMISO: CN2.7 (DAT0), CN6.3, U1.35 (PB14)
SPIMOSI: CN2.3 (CMD), CN6.5, U1.36 (PB15)
SPISCK: CN2.5 (CLK), CN6.4, U1.34 (PB13)
SPKR: D1.A, NY1.P2, U3.16 (OUT1)
TX: U1.51 (PC10)
USBDM: R16.1, U1.44 (PA11)
USBDP: R17.1, U1.45 (PA12)
VBUS: C29.1, D2.A, USB1.P1 (VUSB)
VCC: C2.1, C3.1, C7.1, C9.2, C16.1, C18.1, C19.1, C20.1, C21.1, C22.1, C26.1, C27.1, C28.1, C30.1, C32.1, C34.1, C35.1, C36.1, C37.1, CN2.4 (VCC), CN2.SW1, CN6.1, D1.C, FAN1.3, FAN2.3, FAN3.3, FAN4.3, J4.1, L1.1, NY1.P1, R5.2, SW1.3, SW3.1, SW3.3, U1.1 (VBAT), U1.19 (VCC), U1.32 (VCC), U1.48 (VCC), U1.64 (VCC), U6.5 (VOUT), VREG1.3 (VO), X1.4 (VCC)
VCCA: C4.1, C23.1, C24.1, C25.1, C31.1, C33.1, C39.1, C41.1, C42.1, J1.6, L1.2, U1.13 (VCCA), U2.6 (VCC), U4.1 (V), U5.5 (V)
VCCM: C1.1, C44.1, FAN1.1, FAN2.1, FAN3.1, FAN4.1, J1.2, J1.4, R14.1, U2.4 (IN-), VREG1.1 (VI)
VIN: CN3.3, R14.2, U2.3 (IN+)

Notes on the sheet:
OLED display
SD CARD
diag sync out (to trigger scope)
voltage+current sense low-pass
TXCO
input voltage sense (resistor divider on other board)
diag user input
to power board
seperate/smaller reg for USB power in
USB/serial - diag + programming
power inverter - control board little box challenge

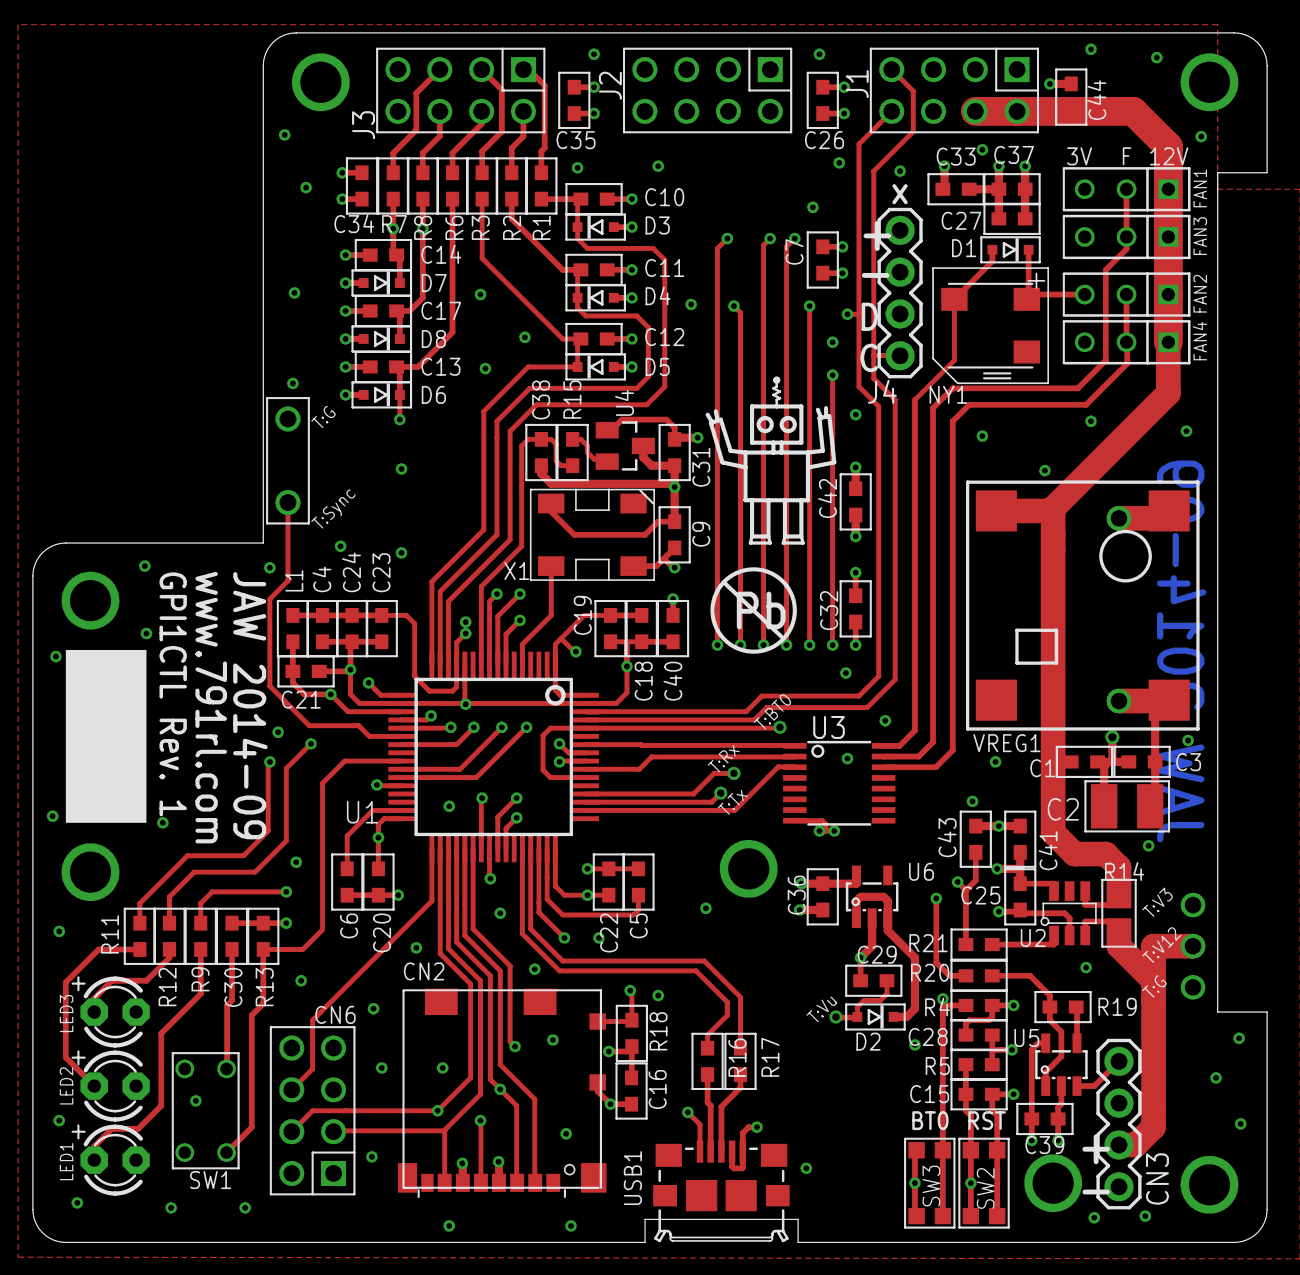
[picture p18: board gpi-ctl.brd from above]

Board: 4 copper layers, 75.0 x 73.5 mm, 101 parts (0 on the bottom side), 65 nets.

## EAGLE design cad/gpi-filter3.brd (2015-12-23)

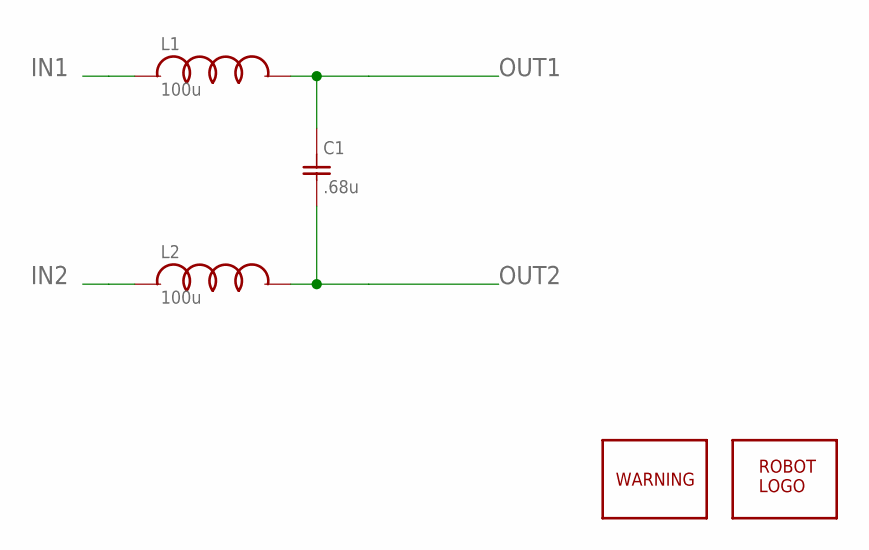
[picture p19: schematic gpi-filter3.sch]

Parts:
C1: .68u; R46KI36804P1M
L1, L2: 100u; AIRD03
U$1: ROBOTMAN-LOGO
U$2: SYMBOL-WARNING

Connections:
IN1: L1.P$1
IN2: L2.P$1
OUT1: C1.P$1, L1.P$2
OUT2: C1.P$2, L2.P$2

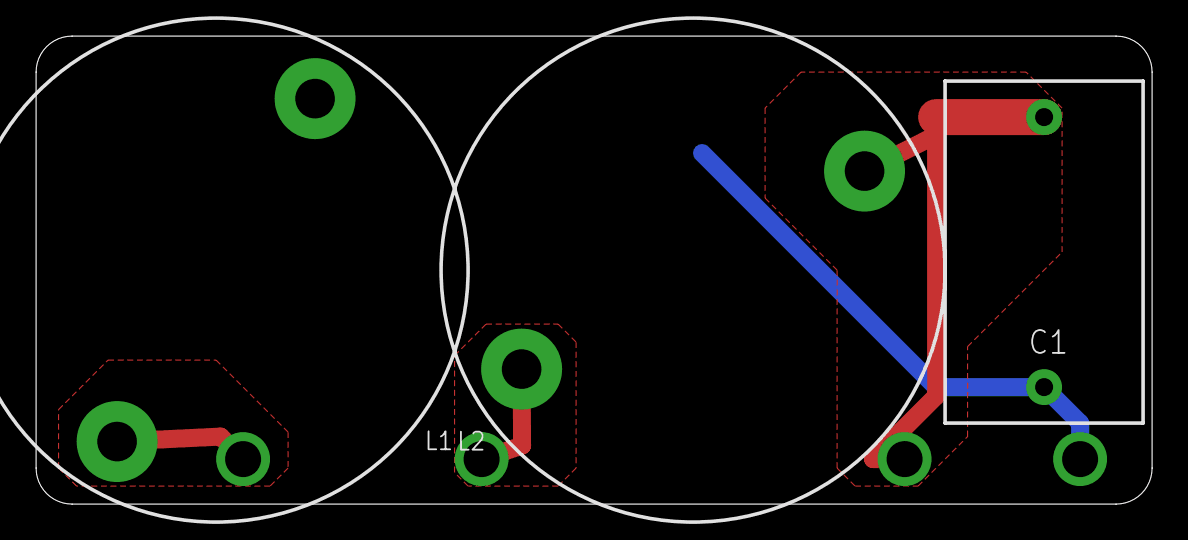
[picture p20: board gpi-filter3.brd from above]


Board: 2 copper layers, 62.0 x 26.0 mm, 5 parts (2 on the bottom side), 2 nets.

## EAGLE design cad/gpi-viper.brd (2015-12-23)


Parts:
C1, C3: .1u; SMD0603
C2: 10u; SMD0603
C4: 1u; SMD0603
C5, C7: 100u; SMD1210
C6: .1u 600V; SMD1210
CN1: 1X4-BIG; 1X04-BIG
CN2: HEADER-1X2.4; HEADER-1X2-THM-WIDE
D1, D2: 600V ultrafast; DO-214AC
D3: DIODESOD-323; SOD-323
D4: 15V; SOD-323@1
L1: 330u; BOURNS2100
R1: 3k9; SMD0603
R2: 10k; SMD0603
R3, R5: 3k3; SMD0603
R4: 590k 500V; SMD1206
U1: VIPER26DIP7; VIPER26-P7
U$1: ROBOTMAN-LOGO
U$2, U$3: SYMBOL-WARNING

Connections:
GND: C4.1, C5.1, C6.2, C7.1, CN1.4, CN2.1, D1.A, D4.A, R5.2
unnamed: C1.1, R1.1
unnamed: C2.1, C3.1, D1.C, L1.P$1, R1.2, R3.2, U1.1 (G)
unnamed: C1.2, U1.5 (COMP)
unnamed: C2.2, D3.C, U1.2 (V)
unnamed: C3.2, D2.C, D3.A, R2.1
unnamed: R2.2, R3.1, U1.4 (FB)
unnamed: C6.1, CN2.2, R4.1, U1.7 (DRAIN), U1.8 (DRAIN)
unnamed: CN1.1, R4.2, R5.1
VOUT: C4.2, C5.2, C7.2, CN1.3, D2.A, D4.C, L1.P$2

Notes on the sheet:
450V DC IN
Vout = 3.3 * (R2+R3)/R3 + Vdiode
12V out
power inverter - 12V board little box challenge
voltage sense - to adc

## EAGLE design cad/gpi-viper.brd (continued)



Board: 2 copper layers, 73.5 x 16.0 mm, 23 parts (3 on the bottom side), 10 nets.

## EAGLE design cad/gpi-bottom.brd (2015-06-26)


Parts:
C1: 1u; SMD0603
CN1: HEADER-3X12MM; HEADER-3X1-2SMD
U1: TEMPERATURE; SOT-23
U$1: ROBOTMAN-LOGO

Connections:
unnamed: C1.1, CN1.1, U1.1 (V)
unnamed: CN1.2, U1.2 (OUT)
unnamed: C1.2, CN1.3, U1.3 (G)


Board: 2 copper layers, 130.0 x 73.5 mm, 4 parts (0 on the bottom side), 3 nets.

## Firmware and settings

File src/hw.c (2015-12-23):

/*
  Copyright (c) 2014
  Author: Jeff Weisberg <jaw @ tcp4me.com>
  Created: 2014-Aug-14 21:06 (EDT)
  Function: 

*/

#include <conf.h>
#include <proc.h>
#include <gpio.h>
#include <pwm.h>
#include <adc.h>
#include <spi.h>
#include <i2c.h>
#include <nstdio.h>
#include <ioctl.h>
#include <stm32.h>
#include <userint.h>

#include "util.h"
#include "hw.h"


/****************************************************************/

DEFVAR(int, bootseqno, 0, UV_TYPE_UL, "boot sequence number")
DEFVAR(uv_str16_t, logfile, "", UV_TYPE_STR16 | UV_TYPE_CONFIG, "auto enable logging to file")

DEFUN(updateboot, "update boot data")
{
    FILE *f;

    f = fopen("bootdata.rc", "w!");
    if( f ){
        fprintf(f, "bootseqno = %d\n", bootseqno + 1);
        fprintf(f, "time      = \"%T\"\n", systime);
        fclose(f);
    }
}

DEFUN(save_all, "save all config data")
{
    save_config("fl0:config.rc");
    save_config("config.rc");
    ui_f_updateboot(0,0,0);
    return 0;
}

/****************************************************************/
void
update_pwm_freq(void){

    // 10kHz +/- 2kHz

    pwm_init(  HW_TIMER_LED_WHITE, 10000 - 2000 + random_n(4000), 255 );
    pwm_init(  HW_TIMER_FAN1,      10000 - 2000 + random_n(4000), 255 );

}


/****************************************************************/

/* NB: timers1+2 => AF(1), timers3+4+5 => AF(2) */

void
hw_init(void){

    bootmsg("hw init:");

    // enable i+d cache, prefetch=off => faster + lower adc noise
    // nb: prefetch=on => more faster, less power, more noise
    FLASH->ACR  |= 0x600;

    // T1,2 => AF(1); T3,4,5 => AF(2), else AF(3)

    gpio_init( HW_GPIO_SWITCH, GPIO_INPUT );
    gpio_init( HW_GPIO_BUTTON, GPIO_INPUT );

    // beeper
    gpio_init( HW_GPIO_AUDIO, GPIO_AF(2) | GPIO_SPEED_2MHZ );
    pwm_init(  HW_TIMER_AUDIO, 440, 255 );
    pwm_set(   HW_TIMER_AUDIO, 0);

    // LEDs
    gpio_init( HW_GPIO_LED_WHITE,  GPIO_AF(2) | GPIO_SPEED_2MHZ );
    pwm_init(  HW_TIMER_LED_WHITE, 10000, 255 );
    pwm_set(   HW_TIMER_LED_WHITE, 0);
    gpio_init( HW_GPIO_LED_RED,    GPIO_AF(2) | GPIO_SPEED_2MHZ );
    pwm_set(   HW_TIMER_LED_RED,   0);
    gpio_init( HW_GPIO_LED_GREEN,  GPIO_AF(2) | GPIO_SPEED_2MHZ );
    pwm_set(   HW_TIMER_LED_GREEN, 0);

    // fans
    gpio_init( HW_GPIO_FAN1, GPIO_AF(1) | GPIO_SPEED_2MHZ );
    gpio_init( HW_GPIO_FAN2, GPIO_AF(1) | GPIO_SPEED_2MHZ );
    pwm_init(  HW_TIMER_FAN1, 10000, 255 );

    // ...
    gpio_init( HW_GPIO_SYNC, GPIO_OUTPUT | GPIO_PUSH_PULL | GPIO_SPEED_2MHZ );

    init_gates();	// start me first
    init_sensors();
    init_timer();
    init_imu();
    bootmsg("\n");

}

void
onpanic(const char *msg){
    int i;

    set_gates_safe();

    set_led_white( 0xFF );
    set_led_red(   0xFF );
    set_led_green( 0 );

    freq_set( HW_TIMER_AUDIO, 200 );
    pwm_set(  HW_TIMER_AUDIO, 0x7F );

    splproc();
    currproc = 0;

    ssd13060_puts("\e[J\e[16m*** PANIC ***\r\n\e[15m");
    if( msg ){
        ssd13060_puts(msg);
        ssd13060_puts("\r\n");
    }
    splhigh();

    while(1){
        set_led_white( 0xFF );
        freq_set( HW_TIMER_AUDIO, 150 );
        for(i=0; i<20000000; i++){ asm("nop"); }

        set_led_white( 0 );
        freq_set( HW_TIMER_AUDIO, 250 );
        for(i=0; i<20000000; i++){ asm("nop"); }
    }
}

/****************************************************************/

// first look on flash, then on card
#define RUN_SCRIPT(file)	(run_script("fl0:" file) && run_script(file))

void
main(void){

    if( RUN_SCRIPT("bootdata.rc") ){
        // could not run rc - play warning tone
        play(32, "[3 d+4>>d-4>> ]");
    }
    ui_f_updateboot(0,0,0);
    mkdir("log");

    RUN_SCRIPT("config.rc");

    extern void blinky(void);
    start_proc( 1024, blinky, "blinky" );

    if( logfile ){
        diaglog_open( logfile );
        diaglog_lores();
    }

    // finally, start the inverter
    init_inverter();

    RUN_SCRIPT("startup.rc");

    // return to shell
}

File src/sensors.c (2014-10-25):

/*
  Copyright (c) 2014
  Author: Jeff Weisberg <jaw @ tcp4me.com>
  Created: 2014-Aug-14 23:03 (EDT)
  Function: analog instrumentation

*/

#include <conf.h>
#include <proc.h>
#include <gpio.h>
#include <adc.h>
#include <nvic.h>
#include <pwm.h>
#include <locks.h>
#include <stm32.h>
#include <userint.h>

#include "util.h"
#include "hw.h"

#define CRUMBS	"adc"
#include "crumbs.h"

#define SR_EOC		2
#define SR_OVR		(1<<5)
#define CR2_SWSTART	0x40000000
#define CR2_ADON	1
#define ADC_VREFINT	ADC_1_17


static lock_t adclock;
static short dmabuf[30];
static short adcstate;
#define ADC_DONE	 0
#define ADC_BUSY	 1
#define ADC_ERROR	-1


// sensor order
#define SEN_0		HW_ADC_VOLTAGE_HIGH
#define SEN_1		HW_ADC_VOLTAGE_OUTPUT
#define SEN_2		HW_ADC_VOLTAGE_INPUT
#define SEN_3		HW_ADC_CURRENT_INPUT
#define SEN_4		HW_ADC_CURRENT_OUTPUT
#define SEN_5		HW_ADC_CURRENT_CTL
#define SEN_6		HW_ADC_TEMPER_1
#define SEN_7		HW_ADC_TEMPER_2
#define SEN_8		HW_ADC_TEMPER_3

/****************************************************************/

// recent sensor values
struct SensorData {
    u_short val;
    u_short lpf;
    u_short hist[3];
};

static struct SensorData sensor_data[9];

int offset_io, offset_ii;


/****************************************************************/

#include "adc_wait.c"
//#include "adc_asyncirq.c"	- too slow
//#include "adc_syncirq.c"	- overruns
//#include "adc_dma.c"	     // - overruns
//#include "adc_dma2.c"	     // - scrambled data

/****************************************************************/


static void
median_filter(struct SensorData *sd){
    short *hist = sd->hist;
#if 0
    sd->val = hist[0];
#else
    // val = median of 3
    if( hist[0] > hist[1] ){
        if( hist[2] > hist[0] )      sd->val = hist[0];
        else if( hist[2] > hist[1] ) sd->val = hist[2];
        else                         sd->val = hist[1];
    }else{
        if( hist[2] > hist[1] )      sd->val = hist[1];
        else if( hist[2] > hist[0] ) sd->val = hist[2];
        else                         sd->val = hist[0];
    }
#endif
}

static inline void
lowpass_filter(struct SensorData *sd){
    sd->lpf = (sd->val + 3 * sd->lpf) >> 2;
}

void
read_sensors(void){
    // read 3x, median filter

    // pick one low-prio sensor to read
    char r = random() & 3, sr;
    switch(r){
    case 0: sr = SEN_5; break;
    case 1: sr = SEN_6; break;
    case 2: sr = SEN_7; break;
    case 3: sr = SEN_8; break;
    }

    adc_get_all(sr, 5+r);

    // unbundle data
    int8_t i,j;
    for(i=0; i<6; i++){
        int si = (i==5) ? 5 + r : i;
#ifdef USE_DMABUF
        for(j=0; j<3; j++){
            sensor_data[si].hist[j] = dmabuf[j*6+i];
        }
#endif
        median_filter(sensor_data + si);
        lowpass_filter(sensor_data + si);
    }

    // emergency fail-safe
    safety_check_boost();
}

static void
calibrate(void){
    int i, to=0, ti=0, tc=0;

    // prime
    for(i=0;i<100;i++) read_sensors();

    // actual io is 0 while idle
    // actual ii ~ ic while idle
    // in Rev.1 ic should be precisely known (but scaled differently)

    for(i=0; i<100; i++){
        read_sensors();
        ti += sensor_data[3].val;	// ii
        to += sensor_data[4].val;	// io
        tc += sensor_data[5].val;	// ic
    }
    offset_io = to / 100;
    offset_ii = ti / 100; // RSN (ti - tc) / 100;

    // bootmsg("ical %d %d\n", offset_ii, offset_io);
}


// returns .1 degrees C
static inline int
temperature(int v){
    // Rev 0
    // sensor is a TC1047
    // 10mV/C
    // 500mV = 0C
    // Rev 1 => LM61, 10mV/C, +600mV

    return ((v * 3300 + 2048) >> 12) - 600;
}

/*     adc * Rt * 3.3
  V  = --------------  << 20   =  Rt(in k) * 256
        3.3k * 4096


        where Rt = Rx + 3.3
*/

// RSN - convert to proper calibrated units V:Q.4, A:Q.8
// RSN - calibrate + temperature compensate
int get_curr_vh(void){    return (sensor_data[0].val * 512270) >> 16; }		// measured 20141018
int get_lpf_vh(void){     return (sensor_data[0].lpf * 512270) >> 16; }		// "
int get_curr_vo(void){    return (sensor_data[1].val * 150678) >> 16; } 	// measured 20141015
int get_lpf_vo(void){     return (sensor_data[1].lpf * 150678) >> 16; } 	// "
#if 0
int get_curr_vi(void){    return 192;    return sensor_data[2].val; }		// not hooked up
int get_lpf_vi(void){     return 192;    return sensor_data[2].val; }		// not hooked up
#else
int get_curr_vi(void){    return (sensor_data[2].val * 150678) >> 16; } 	// estimated
int get_lpf_vi(void){     return (sensor_data[2].lpf * 150678) >> 16; } 	// "
#endif
int get_curr_ii(void){    return ((sensor_data[3].val - offset_ii) * 100663) >> 14; }
int get_lpf_ii(void){     return ((sensor_data[3].lpf - offset_ii) * 100663) >> 14; }
int get_curr_io(void){    return ((sensor_data[4].val - offset_io) * 100663) >> 14; }
int get_lpf_io(void){     return ((sensor_data[4].lpf - offset_io) * 100663) >> 14; }

int get_curr_ic(void){
    // LMP8640 Gain = 100, R = 0.01
    // mA = v * 3.3/4096 * 1000
    // Q8 = v * 3.3/4096 * 256
    return (sensor_data[5].val * 845 + 2048) >> 12;
}
int get_lpf_ic(void){	return (sensor_data[5].lpf * 845 + 2048) >> 12; }


int get_curr_temp1(void){ return temperature(sensor_data[6].val); }
int get_curr_temp2(void){ return temperature(sensor_data[7].val); }
int get_curr_temp3(void){ return temperature(sensor_data[8].val); }

int
get_max_temp(void){
    // determine hottest temp
    int t  = get_curr_temp1();
    int tt = get_curr_temp2();
    if( tt > t ) t = tt;
    tt = get_curr_temp3();
    if( tt > t ) t = tt;
    return t;
}

DEFUN(testsensors, "test sensors")
{
    short i, j;

    while(1){
        read_sensors();
        printf(" vh   vo   vi   ii   io   ic   t1   t2   t3\n");
        for(i=0; i<3; i++){
            for(j=0; j<9; j++){
                printf("%04.4x ", sensor_data[j].hist[i]);
            }
            printf("\n");
        }
        for(i=0; i<3; i++){
            for(j=0; j<6; j++){
                printf("%04.4x ", dmabuf[i*6 + j]);
            }
            printf("\n");
        }

        printf("\n");
        if( check_button() ) return 0;
        sleep(1);
    }
}

DEFUN(testpowersensors, "test power sensors")
{
    while(1){
        read_sensors();
        printf("\e[J");
        printf("vi %5d ii %4d\n", get_curr_vi(), get_curr_ii() );
        printf("vo %5d io %4d\n", get_curr_vo(), get_curr_io() );
        printf("vh %5d ic %4d\n", get_curr_vh(), get_curr_ic() );
        printf("\n");
        if( check_button() ) return 0;
        usleep(100000);
    }
}

DEFUN(testvi, "test vin")
{
    while(1){
        read_sensors();
        printf("\e[J\e[17mVI %d\n", get_curr_vi());
        if( check_button() ) return 0;
        usleep(100000);
    }
}
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

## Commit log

2014-08-10 boards rev 0
    [gpi-ctl.brd, gpi-ctl.sch, gpi-pwr.brd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]
2014-08-12 better output filter
    [gpi-pwr.brd, gpi-pwr.sch]
2014-08-13 tweak sent to fab
    [gpi-ctl.brd, gpi-ctl.sch, gpi-pwr.brd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]
2014-08-23 viper package
    [gpi-ctl.sch, gpi-pwr.brd, gpi-viper.brd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]
2014-08-24 viper26, clearances, diodes
    [gpi-viper.brd, gpi-viper.sch]
2014-09-04 tweak text
    [gpi-ctl.brd, gpi-ctl.sch, gpi-pwr.brd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]
2014-09-05 adc, init
2014-09-06 gate snubbers
    [gpi-pwr.brd, gpi-pwr.sch]
2014-09-07 op-amps on v-divs
    [gpi-pwr.brd, gpi-pwr.sch]
2014-09-07 temp sensor
    [gpi-ctl.brd, gpi-ctl.sch]
2014-09-07 op amp on v-div
    [gpi-ctl.brd, gpi-ctl.sch]
2014-09-07 vcca to conn
    [gpi-ctl.brd, gpi-ctl.sch]
2014-09-07 sync, green led
    [gpi-ctl.brd, gpi-ctl.sch]
2014-09-08 zoned grounds
    [gpi-pwr.brd, gpi-pwr.sch]
2014-09-11 lmp current sense
    [gpi-ctl.brd, gpi-ctl.sch]
2014-09-11 swap layers
    [gpi-ctl.brd]
2014-09-14 output filter
    [gpi-ctl.brd, gpi-ctl.sch, gpi-filter.brd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]
2014-09-16 move leds, hole size
    [gpi-ctl.brd]
2014-10-12 missing wire
    [gpi-ctl.brd]
2014-10-12 bigger cap
    [gpi-ctl.brd, gpi-ctl.sch]
2014-10-13 diode silk
    [gpi-pwr.brd, gpi-pwr.sch]
2014-10-25 adj freq to avoid saturation
    [gates.c]
2015-12-23 pdfs, comments
    [gpi-align.brd, gpi-ctl.sch, gpi-filter3.brd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]
2016-03-11 revert opamp, tweak
    [gpi-ctl.brd, gpi-ctl.sch, gpi-pwr.brd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]
2016-03-12 rename files
    [gpi-filter0.brd, gpi-filter0.sch, gpi-filter1.brd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]
2016-03-12 add schematic pdf
2016-03-13 readme, clean
    [gpi-pwr.brd, gpi-pwr.sch]
